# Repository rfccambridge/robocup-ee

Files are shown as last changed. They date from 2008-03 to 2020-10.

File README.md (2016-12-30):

## Build Environment Installation

- Make sure you have clang-format installed: 
  ```
  apt-cache search clang-format
  sudo apt-get install clang-format-<version>
  ```
- `source /opt/ros/kinetic/setup.bash`
- `cd <your robocup directory>/catkin_ws/src`
- `catkin_init_workspace`
- `cd <your robocup directory>/catkin_ws`
- `catkin_make`
- `source <your robocup directory>/catkin_ws/devel/setup.bash`
- Make sure running `echo $ROS_PACKAGE_PATH` prints something similar to `/home/<your_user>/catkin_ws/src:/opt/ros/kinetic/share:/opt/ros/kinetic/stacks`

## Setting Up Your Own Branch To Work In

- `git checkout -b <your name>_branch`
- Now, all changes you make will affect only your environment and no one else's.

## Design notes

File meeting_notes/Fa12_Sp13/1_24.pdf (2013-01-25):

The EE and CS subteams had a meeting on Thursday. Minutes are below, with some relevant notes (section "Mechanical fixes needed") to the ME subteam.

Driving with game controller:

Used remote controller to drive robot. Just use serial control and click "connect to joystick." Make sure it's matched up to the correct robot id.

We noticed strange smell from Jayne, but from River. We couldn't isolate the problem and eventually didn't notice the problem anymore.

Shut-down problem:

At the all-team meeting we noted that a robot would sometimes shut down while driving. We thought it was because the robot was drawing too much current from the batteries when accelerating, thus causing the robots to shut down to avoid permanent damage. We planned to use firmware to limit acceleration.

However, upon further investigation, we found that one robot had this problem only when (1) the kicker board was in and (2) the black cap of the robot was screwed on. This suggests that the cap and kicker board is pushing down and causing a short circuit as the robot is moving, though we're not exactly sure where the sort circuit may be.

We noticed that the boards were wobbly. Rui suggested we hot-glue the boards in at the header pins, so that they're more stable.

More investigation is needed in order to find the exact cause and how to prevent it, and whether this problem only occurs for only that robot, or only that kicker board. EE plans on coming back to Harvard for further trials before the all-team meeting.

Mechanical fixes needed:

- 2 motors are kind of weird - one has a loose gear, the other we may have killed. Both motors are labelled
- 1 robot lacks a plunger for the kicker
- 2 robots don't have the BB set up properly

EE plans on going back on February 9th to test the driving. Is it possible to have these robots - at least the motors - fixed up by then?

Decreasing modularity of electronics:

In the long term, we may need some redesign of the boards. It was suggested to decrease modularity. The boards often don't have too many problems once properly built up, and having fewer boards would decrease the chance for boards randomly touching and short circuiting each other. We would probably hold off the design until after the 2013 competition. Some possible approaches are
- all circuitry on the motherboard
- FPGAs
- PSoC (http://www.cypress.com/?id=1353)

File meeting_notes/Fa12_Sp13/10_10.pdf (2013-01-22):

Minutes:

Recap Last week: Kicker/ Aus
Kicker board – charges caps and sends energy to solenoid (kicker) Auxiliary kicker – a control board that tells the kicker when to kick, when to charge
MOSFET – component used in aux; we use nmos (rather than pmos)
- gate – when voltage between gate and source large enough, current flows from drain to source
- drain
- source

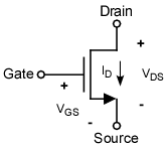
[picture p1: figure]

- further reading: http://en.wikipedia.org/wiki/MOSFET#Modes_of_operation

This week: Brushless
Next Week: firmware

DRC check for eagle tutorial – errors are ok, you'll notice if it is a glaring mistake
ERC – checks schematic versus layout – try to get no errors, which mean that things are not connected; warnings are ok

Brushless board:
– 4 boards on each robot
– each board controls 1 wheel
– communicates with computer to drive wheel – 3 pairs of mosfets
– high side mosfet
– low side mosfet

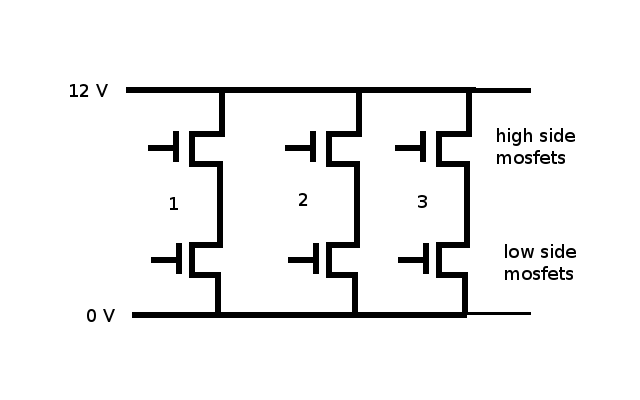
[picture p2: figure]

– can never turn high side and low side mosfet on for the same totem pole
– energizing any pair can get a certain phase

Motor:
– we use brushless motors
– magnet and set of coils
– when a certain set of coils are energized, they induce magnet to go in certain direction
– paste link here for more info
– 3 phases
– hall sensors in motor detect when motor has reached a certain position; will signal that next phase need to be energized

Controlling speed
– You can consider: a variable power source; however, that's difficult to make
– Alternatively: use a 12 volt source, but use a switch to apply the 12 volts for a percentage of the time
– Duty Cycle: the percentage of time the voltage is applied (50% duty cycle for a 12 volt source is equivalent to applying a 6 volt source)

– We keep frequency constant

Oscilloscope Demonstration:
– as the pwm increases, the length of time that the signal is on is longer, also the speed is increased
– note that there are some vias on the board that exist purely as useful probing spots for the oscilloscope probe

Schematic of Brushless Board
– Leftmost panel of schematic shows header pins
– pin2 = 5V
– pin 3, pin4 = QEB, QEA = encoder signals → let us calculate how quickly the motor is going
– BBID0, BBID1 – tells brushless board 1 to do what, tells brushless board 2 what to do; because same signal gets sent to all board (multiplexed), so we need a way to separate the commands
– Hall3, Hall1, Hall2 – hall effect sensors are built into motor; depending on which signal is high, we know which position the motor is in; firmware reads this, and then instructs the mosfets (from the brushless board) to change phase, so that the wheel will turn to another position

Hold on: Hall effect sensor tells us the position information. Encoder also tells us position information. Why both?
Hall effect is very precise – so we use it to tell when to change phases; reducese jittery
Encoder – used to estimate speed and high speed information; in our control loop, we use the encoder to control the speed of the motor

– BOTID0, BITID1, BOTID2, BOTID3 – robot ID;
– question, why do we use 4 ID's?
– For future expansion, so we can suport up to 16 robots. Also, if we ever get 10 robots and want to play them against each other, we can have a unique ID for all of them
– TX, RX – singals, from/to antennae and transmitter
– are signals incripted?
– No, but they are modulated on to carrier frequency
– PH3, PH2, PH1 -
– pin 1, quiet ground – for things that draw small current like microcontroller;
– pin 24, 25 – PE = power ground; draws large current
– if microcontroller is connected to power ground -

Bypass capacitors – supply is noisy; to reduce noise, we add capacitors across ground to act like a low pass filter
Low pass filter:
– http://en.wikipedia.org/wiki/Low-pass_filter#Passive_electronic_realization
– various values: 100 mF and .1 mF in parallel – why?
– B/c 100 mF has bad frequency response (no longer looks like 100 mF at high frequencies, will look like an inductor instead)
– putting 0.1 mF in parallel reduce

Middle Pane:
– microcontroller --- let's ignore this for not

Right pane
– driver – acts as voltage commander
– pins on left receive commands from microcontroller (0-5V)
– pins on right are same signals as commands from microcontroller, but get sent out at 0-12 V – add link to datasheet

Questions
– What are diode and capacitro for
– they are part of a “bootstrap circuit” which help us to get the 12 V exactly
– what are resistors between 12V gate and gate of mosfet for
– limit the current to mosfet; we want to do this b/c the mosfet has a parasitic capacitance in it;
– sense resistor
– monitor current by monitoring voltage across here;

Projects
– Kicker – Erwin, Ben, Manny
– Dribbler – David G, David K, Markus
– Acceleration – Manny, Erwin
– Debugging – Erwin, Markus, Manny, Ben

Timeline
– feb, so that CS has time to implement

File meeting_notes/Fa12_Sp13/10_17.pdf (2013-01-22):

This week in summary: Brief introduction
Next week: take the robot apart and put it back together

Firmware:

(1) Install the following:
IDE: MPLab X
Compiler: XC8, XC16

Get the free versions. If it prompts you for a license key, click "next" and it will ask you to select the free version.

(2) Create a new project (use code from robocup repository):

(2a) The Aux board requires the following project setup:

Family: PIC18F4431
Tools: PICKit2
Compiler: XC8
Right click project once project is created | Add Existing Files
Add these files (and only these files) from robocup-ee/firmware:
- bemixnet.c
- bemixnet.h
- mainLogic_newestBB_no_false_positives.c
- pins.h

(2b) The brushless requires the following project setup: Family: dsPIC30F4011
Tools: PICKit2
Compiler: X16
Right click project once project is created | Add Existing Files
Add these files (and only these files) from robocup-ee/firmware:
- bemix_v2.n
- bemix_v2.h
- main_v2.c
- pins_v2.h

Aux uses 8-bit microcontroller
Brushelss uses 16-bit microcontroller - recently upgraded to nicer (faster) microcontroller

--> microcontrollers have to be programmed slightly differently

Process for loading code onto board:

Note the following:
- on board, there is a 5 pin header pin
- there is a programming cable

Process:
1. plug in board to power (plug it into the robot, with the robot turned on)
2. plug in programmer to the header pin, with the arrow on the programmer pointing to pin 1
3. build project (there is a button in the IDE)
4. program the board (button)
5. toggle power
Order:
Hint: never plug things in backwards! signals go to specific places, and applying the wrong signal to the wrong pin can destroy a board

All brushless boards faces front. Aux board faces front. Kicker board faces the back (to make it fit). Yellow cable to motor. The connector has a set of "tabs" that you need to loosen in order to remove the cable. Silver side faces up.
Encoder cable. You'll notice on the motherboard, the one pin is marked 1, the other pin is marked 4. On the connector, there is line that is marked black or red. make sure the black or red line is matched up to pin 1.

Random question when looking at schematic:
Thermal - a thin traces that connect a component to the main part of the trace. makes it easier to solder b/c there is less heat loss. However, our traces are usually thin enough that we don't have to lose about heat dissipation while soldering.

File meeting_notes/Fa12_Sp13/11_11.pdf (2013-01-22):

Here are notes from today's meeting if you had to leave early or couldn't make it out:

All-team meeting, scrimmage

We plan to have a all-team meeting at Harvard toward the beginning of December to see the robots driving around and to try to get a two-on-two game going on. But for that, we need the following fixed up

- break beams
- auxiliary kickers
Break Beams

The break beams are used to detect when the ball is in front of the kicker, so the robot knows exactly when to kick.

An old system we tried was a reflective break beam sensor. It did not work well because the ball was not so reflective, it was dependent on ambient light conditions, and was sensitive to the ball coming in from a variety of angles.

The current system places the emitter LED and receiver on the left and right side of the ball. The emitter sends infrared light at a certain frequency, which the receiver looks for. When the beam is broken, the receiver sends an active low signal. This is slightly more robust, though we will have to put a lot of effort into placing the emitter and receiver.

Auxiliary Kicker

We ran into some problems demonstrating the break beam boards because the aux kicker boards (which run the firmware for the break beams) have been having trouble (1) getting programmed or (2) receiving signals from serial control.

We believe these problems are due either to (1) faulty chips or to (2) the fact we upgraded our programming IDE and there may be some conflicts. Rui's looking into the IDE, but if he doesn't identify any problems, we'll order a new set of chips and replacing them.

Solenoid

I believe last week Markus and David(?) played around with the kicker. They raised it a bit, so that the center of the kicker hit the ball. A maximum of 4 m/s was attained, doubling the energy being delivered to the ball.

Markus built up a new shaft for the solenoid, which included a magnetic material for the shaft instead of a aluminium. However, when we tried to kick, it didn't work.

Plan for next week:

- debug/rebuilt aux kicker boards
- get break beams working
- test Markus's new designs

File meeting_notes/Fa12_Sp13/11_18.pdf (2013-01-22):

Also, remind me to add you to the MechE list if you want to spy on what they do!

Minutes:

- should be electrically fit for all-team meeting!
- just need to mount breakbeams
- next meeting is in 2 weeks
- keep your repository up to date - pull the changes that we committed today.
- have a great thanksgiving break!

Auxiliary Kicker

- there was a problem with code in the repository, not the the new IDE. When Rui used the old code from the computer (back when we used subversion as a repository), and it worked. Repository is now updated.
- some aux kickers still seem to have a write protection on them, so we have to replace those pics next time

Breakbeam

- works now that the aux board's pic has been fixed!
- added an arbitrary delay before the receiver looks for sensor signal, so that the kicker would not immediately kick.

Dribbler

- when set to 0, the pin PWM4 would output a constant 0V
- when set to anything else, PWM4 would output a constant 5V
- perhaps we're configuring some registers incorrectly?
- to do: read section 15 and 17 of datasheet (PIC18F4331)

For next meeting:

- mount break beams
- replace pics on aux kickers
- figure out the pwm registers to the dribbler
- Markus's solenoid shaft?
- make sure we can assemble a robot with all working components?

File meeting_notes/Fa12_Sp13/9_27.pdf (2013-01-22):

Minutes – 9/23/12 EE Sub-meeting

Eagle
- Download Eagle
- google: “cadsoft eagle”. The first link should bring you to the website.
- under “Downloads” there should be instructions for installing a free version
- There are 2 views
- schematic: pick components and wire them together
- board layout: layout the components as they would be placed on a board
- Eagle will generate files that can be sent out to manufacturers to print circuit boards
- Useful for future projects, in which we might create simple boards to help gather data for other subteams

Git
- Revision Control Software – allows us to concurrently make changes while avoiding conflicts; keeps track of old versions; learn more here: http://gitimmersion.com/
- To get access our git repository, make an account here: http://github.com then send Lisa (liulisa@mit.edu) your username
- If you use windows, you should also download this: http://code.google.com/p/tortoisegit/
- For macs and ubuntu, e-mail Rui or Lisa

Kicker Board
- controls kicking of the ball
- computer commands board to charge capacitor
- takes 2-3 seconds to charge
- audible humming noise b/c the board flips a switch to increase voltage (more explanation on this later, or read wikipedia page on buck converters)
- another computer command sends the energy through a solenoid, which creates a magnetic field, which pushes forward a plunger, which hits the ball
- vaporize resistor demonstration
- Together the capacitors are 3 milliFarads and charge up to 250 V! For capacitors energy = (1/2)*C*V^2 → this is “like getting punched”
- Instead of sending energy to solenoid, we placed a 5 kOhm resistor at the load terminals
- Some equations:
- V = I*Resistance
- Power = I*V
- 12.5 Watts across the resistor which is rated for 0.25 Watts.
- Resistor smoked, then exploded. Remains are yet to be found.
- Discussion about how to repeat the experiment with a hot dog.
- Conclusion: it would be messy
- Takeaway: the capacitors are dangerous
- neon light indicates when capacitors are charged
- use discharge button, hold down for 5 seconds after light goes out before handling robot again

Possible projects
- circuits boards – other subteams need to gather stats
- debugging circuit boards (using oscilloscope)
- firmware?

Next few weeks:

9/30 – More about Kicker/Aux board
10/7 (or maybe later on this 4-day weekend) – Brushless boards 10/14 – Firmware

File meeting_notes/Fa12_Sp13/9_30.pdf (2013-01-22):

Thanks for coming to the meeting today. For those of you who couldn't make it, here are some points from today's meeting:

Think about small projects you want to do to improve the robot
- Suggestions: measuring kicking speed / distribution, optimizing efficiency of energy transfer from capacitors to ball, multiple kickers / chip kicking, optimizing dribbler, optimizing break beam, characterizing robot acceleration
- Work in groups if you want
- Think about small projects you want to do to improve the robot
- Suggestions: measuring kicking speed / distribution, optimizing efficiency of energy transfer from capacitors to ball, multiple kickers / chip kicking, optimizing dribbler, optimizing break beam, characterizing robot acceleration
- Work in groups if you want
- Auxiliary kicker and kicker boards form a subsystem on the robot for charging up the capacitors and kicking the ball
- Auxiliary kicker board communicates with off board computers
- Tells kicker board to charge capacitors / kick ball
- Tells dribbler to turn on/off
- Kicker board controls charging the kicking capacitors and kicking the ball
- Charge the capacitors by storing energy in transformer and dumping onto capacitor
- Kick the ball by dumping energy from capacitors into solenoid
- MOSFETs are switches used to turn on/off current
- MOSFETs have 3 terminals: gate, drain, source
- Raise voltage at gate to turn on switch between drain and source\
Lower voltage at gate to turn off switch

Please do the Eagle tutorial! I've attached the tutorial again in this email. If you still don't have access to the Robocup EE files on Git, I'll show you next meeting.

Next week is a 4-day weekend, and we'll send out a Doodle to see what times people are available. We'll be talking about the brushless boards.

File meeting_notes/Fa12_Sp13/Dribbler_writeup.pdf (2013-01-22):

Dribbler Motor Writeup
Lisa Liu
January 10th, 2013

Purpose: In the Robocup competition, many teams employ a dribbler in order to put backspin on the ball so that the robot controls the ball while moving. Although RFC-Cambridge installed a prototype of the dribbler, it has not yet been used in gameplay. For the Fall '12 semester of Power Electronics (6.131), my final project was to get the dribbler running in response to signals from the microcontroller, so it could put backspin on the game ball.

Background: The dribbler mechanism is composed of a DC dribbler motor and a rubber tube. The tube is placed onto an spinning axis, which is connected to the motor with an elastic band. Therefore, when the motor spins, so does the tube, which spins the ball backward.

The DC motor spins at a rate proportional to the applied voltage. That is, w = k*V, where w is the rotational velocity; k is the motor constant; and V is the voltage applied. We can vary the voltage using a PWM signal.

The PWM signal comes from a microcontroller on the auxilliary kicker board. However, the microcontroller only outputs 0 and 5 V, so there is some additional circuitry on the auxilliary kicker board which buffers the 5 V up to 12 V.

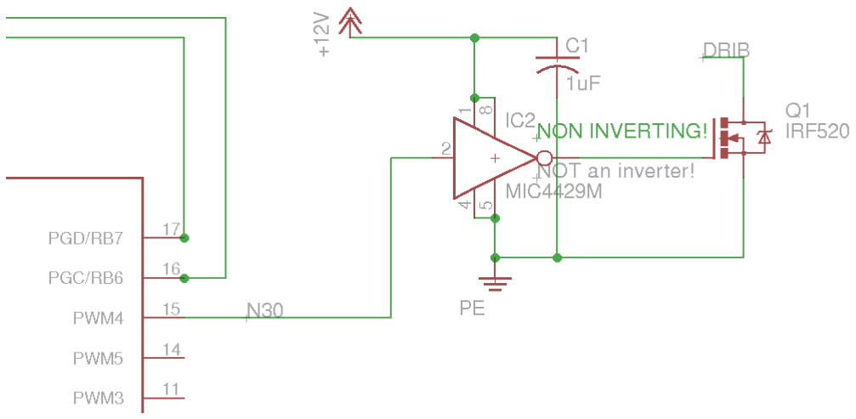
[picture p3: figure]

Figure 1. The microcontroller on the auxillery kicker board outputs a PWM signal from pin 15 (PWM4) which goes to the MIC4429M MOSfet driver. The MIC4429M boosts the 0-5 V signal from the microcontroller up to 12 volts.

The DRIB signal is connected to the motherboard, where the motor terminals are. One terminal is connected to the DRIB (which is relabeled as “DRIB-” on the motherboard schematic). The other terminal is connected to V+, which is the positive terminal of the battery.

In gameplay, we would like the microcontroller to process radio commands. When it receives a command to run the dribbler motor, the dribbler motor will ideally put backspin on the ball.

Problem: There are some mechanical problems with the design. That is, the tube doesn't turn so easily, which may make the load too much for the motor. There are varying sizes of elastics, and not all (*cough* very few) of them are conducive to making the tube spin.

A minor electrical issue was that the motor was not properly speced to the robot. The motor could take voltages up to 24 volts, but the robot provided only 12 volts. Even though the motor could backspin the ball at 12 volts, there was concern that the full potential of the motor was not utilized.

The main problem encountered at the EE submeetings is getting the microcontroller to output a PWM signal at all. We suspected that the microcontroller was incorrectly programmed.

Project:

Boost Converter

In speaking to bakerl from ME, I found out the ME subteam is updating the dribbler design and getting a new motor, which is more properly speced to the robot. This is perhaps the better solution, as building the boost converter requires extra PCB space and relatively large capacitors, which might not fit in the robot and would certainly weigh the robot down. Therefore, this portion of my project is no longer relevant, but may be useful for learning or for future reference.

I built a a boost converter which boosted the voltage to a higher voltage, which depended on the duty cycle according to V_out = V_in /(1-D).

However, the PWM signal only controlled the amount of boosting, and otherwise required the motor to always be connected to the battery. This is unideal because unneeded dribbling will waste battery energy. Therefore, I added a LM555 timer in one-shot monostable mode to act as a switch; when there was no PWM, the motor was disconnected from battery, else it let the PWM signal power the the robot.

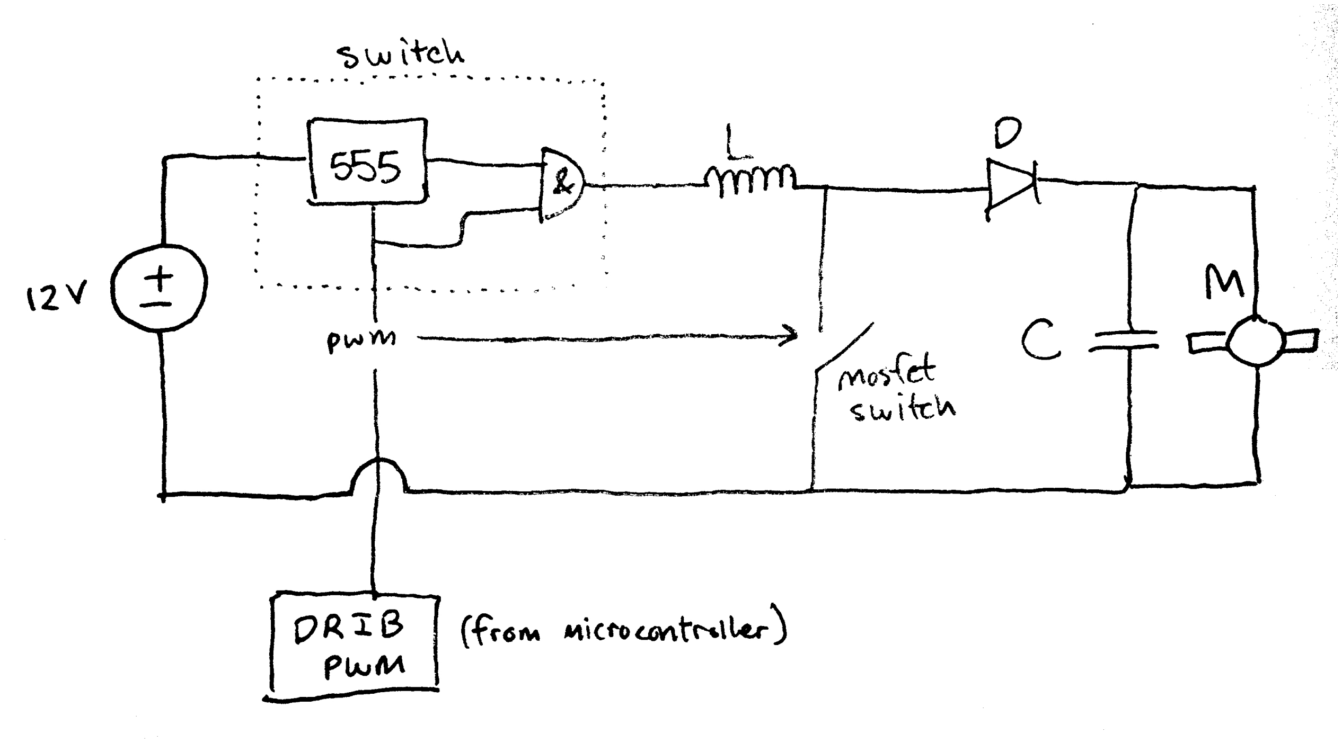
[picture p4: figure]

Figure 2. When the 555 is set up in one-shot monostable mode, it will output a HIGH signal when it detects a falling edge on the input pin. The duration of the HIGH signal depends on an external capacitor and resistor.

Programming the microcontroller:

During subteam meetings, we were unable to successfully program the microcontroller to PWM. The key register that needed to be adjusted was PWMCON0. This register needed to be adjusted so that PDC2 would be in complementary mode. Previously, it was in independent mode, which means that PWM1 would output a signal, but PWM4 would be left hanging. PTPERH, PTCON1, and PDC2L (and perhaps a few other registers) control the frequency and duty cycle of the signal.

In a future implementation of the auxilliary kicker board, it may be simpler to use the pins for PWM1, PWM2, or PWM3, which do not require the complementary mode bit to be set.

Measurement:

During subteam meetings, we tried to measure the output of the microcontroller by placing the oscilloscope probes directly on the V+ and DRIB- terminals. While we noticed V+ always as 12 volts, as expected, however, DRIB- was less consistent.

The problem in our method of measurement is that DRIB- is left hanging. That is, when the PWM signal is HIGH, the MOSfet connects DRIB to ground, which is what we expect. However, when the PWM signal is LOW, the MOSfet leaves DRIB hanging, giving output a signal which is neither HIGH nor LOW. Therefore, we need a pullup resistor in order to measure any sort of meaningful signal.

A naïve thought is to use the resistance of the motor as a pull up resistor. However, as we explore in the next section, directly plugging the motor into the motor terminals doesn't work.

Motor:

When I used a pull up resistor on the DRIB terminal, the output of the microcontroller was a PWM signal exactly as we want it to be. However, when we use a motor instead of a resistor, the output looks extremely irregular.

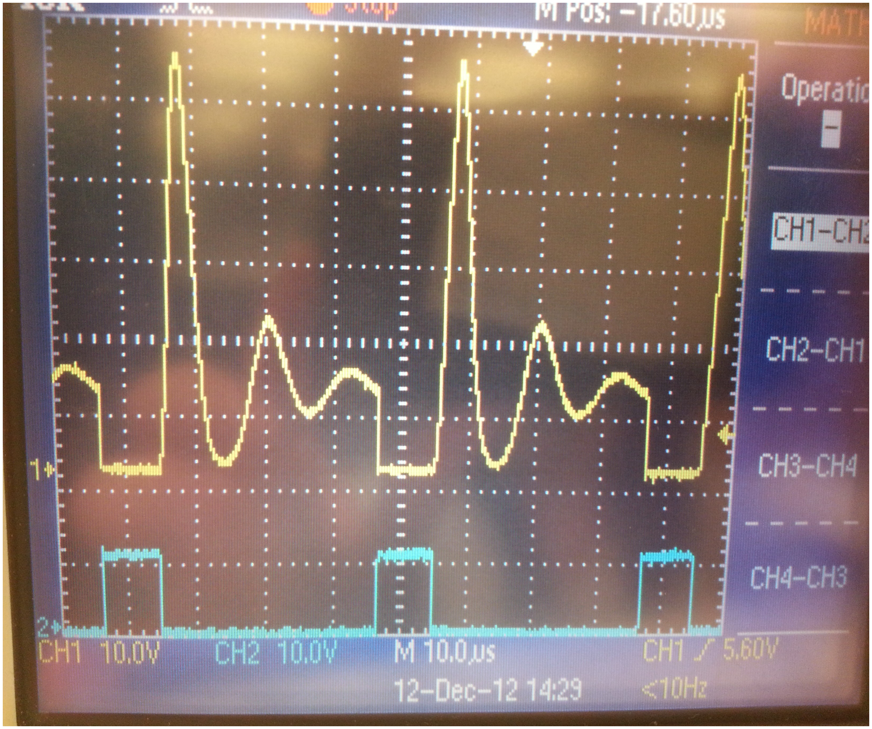
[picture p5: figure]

Figure 3. The blue signal is the signal between the MOSfet driver and the MOSfet. The yellow signal is the voltage across the motor; it reaches voltages up to 50 volts and displays significant oscillations.

The oscillations are due the th inductance of the motor, which creates an LRC circuit. This adds reasonance and oscillation to the circuit, explaining the 50 V peak and the inability of the DC motor to operate properly.

Therefore, a diode should be placed across the motor, between the DRIB- and V+ terminals, facing the DRIB- terminal, in order to stop the capacitor from charging and creating the reasonant circuit.

Conclusion:

A boost converter is not needed. But perhaps in future implementations of the boards, the following changes should be made:

- Auxillery board should be use PWM1, PWM2, or PWM3, before using PWM4.
- Motherboard should put a diode across the dribbler terminals.

A boost converter is not necessary, since it seems 12 V is enough to provide backspin on the ball. We will leave it up to the ME subteam to get the ball rolling.

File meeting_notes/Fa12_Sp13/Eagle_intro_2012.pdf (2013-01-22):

Getting

to

know

Eagle

1. Download

(http://www.cadsoft.de/freeware.htm)

and

install

Eagle.
2. We

are

going

to

design

in

Eagle

a

board

to

test

the

kicker

board.

Here

is

the

circuit

that

we

will
work

with:

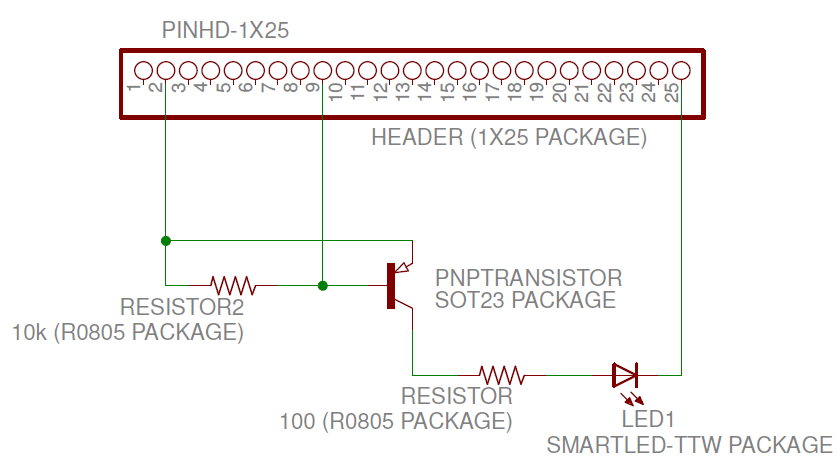
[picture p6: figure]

The

rectangle

with

25

pins

at

the

top

is

a

set

of

header

pins

similar

to

the

header

pins

on

each
board

that

plugs

into

the

motherboard

on

the

robot.

Pin 2

is

a 5V

supply

pin,

pin

9

is

called

the
DONE

pin,

and pin

25

is

the

ground

(0V)

pin.

This

circuit

is

supposed

to

turn

on

the

LED

when

the
kicker

board

finishes

charging

the

capacitors.

Before

the

capacitors

are

done

charging,

pin

9

is

at
5V.

After

the

capacitors

are

done

charging,

pin

9

goes

down

to

0V,

which

turns

on

the

PNP
transistor.

The

PNP

transistor

acts

like

a

switch.

When

the

left

terminal

is

at

5V,

the

switch

is

off.
When

the

left

terminal

is

at

0V,

the

switch

is

on,

which

allows

current

to

flow

in

the

direction

of
the

arrow,

from

the

top

terminal

to

the

bottom

terminal.

In

our

case,

current

flows

from

pin

2,
through

the

PNP

transistor,

through

the

LED,

to

pin

25.

This

turns

on

the

LED

when

the
capacitors

are

done

charging.

In

this

project,

we

will

create

this

circuit

in

Eagle

and

design

a

printed

circuit

board

(just

like

the
boards

that

go

into

the

robots

right

now).

Circuit

Schematic

a. Open

up

Eagle

and

select

File

-‐>

Open

-‐>

New

Schematic
b. Add

all

of

the

parts

in

this

circuit

to

the

schematic

using

the

Add tool

(looks

like

a

“D”)

on
the

left toolbar.

Each

part

in

the

diagram

above

has

a

part

name

and

a

package

name.

In

the

Add tool

you

should

search

for

the

part

name

and

then

select

the

part

that

has

the

same
package.
a. After

you

have

found

the

part,

you

may

double

click

on

it

and

it

will

show

up

in

the
schematic.

Click

to

place

the

part

where

you

want

it.

You

can

rotate

the

part

before
placing

it

down

by

right

clicking.
b. At

any

time,

you

may

press

Escape

to

exit

the

tool.
c. To

move

any

item

after it

has

been

placed,

use

the

Move tool.

To

rotate

any

item,

first
select

it

using

the

Move tool

and

right

click

to

rotate

it

90

degrees.
a. Each

item

may

be

selected

using

any

tool

by

clicking

on

the

item’s associated
crosshair.

Notice

that

each

item

has

a

crosshair.

Don’t

just

click

on

the

item

itself,
because

while

most times

the

crosshair

for

the

item

is

in

the

center

of

the

item,
many

times

it

is

not.
b. If

you

click

too close

to

more

than

one

crosshair,

Eagle

does

not

know

which

item
you

selected.

In

this

case,

Eagle

will

highlight

one

of

the

items

it

thinks

you

selected.
If

that

is

the

item

you

want,

left

click

again.

If

not,

right

click

and

Eagle

will

highlight
another

item

it

thinks

you

selected.
d. You

can

find

and

edit

the

name/value

of

any

item

by

using

the

Info tool

(looks

like

an

“i”)
and

clicking

on

the

item.
a. After

clicking

on

any

item,

in

the

Properties window,

you

can

select

the

Smashed
option

to

separate

the

item

and

its

name/value

as

separate

items.

Then,

you

may
move

the

name

or

value

of

the

item

independently

of

the

item

itself

(note

that

the
name

and

value

will

have

individual

crosshairs).
e. You

may

duplicate

an

item

by

using

the

Copy tool

and

clicking

on

the

item

you

want

to
duplicate.

Note

that

you

should

use

the

Info tool

to

change

the

name/value

of

the
duplicated

item

to

something

unique.
f. Add

wires

as

shown

in

the

diagram

using

the

Wire (looks

like

a

diagonal

line)

tool.

At

any
time,

you

may

press

Escape

to

exit

the

tool

and

stop

drawing

more

wires.
a. The

wires

should

connect

appropriately.

To

check

that

two

wires

are

connected,
make

sure

they

have

the

same

names

using

the

Info tool.
b. You

can

force

two

intersecting

wires

to

be

connected

by

using

the

Junction tool
(looks

like

a

green

dot).

In

the

diagram,

I

have

placed

two

green

dots

at

two
different wire

intersections

to

force

a

connection.

Board

Layout

After

creating

the

circuit

schematic,

click

on

the

Board button

at

the

top

to

switch

to

board

view.
(Create

a

new

board

if

Eagle

asks

you

to.)

You

will

see

all

the

parts

that

you

placed

in

your

circuit
in

the

board

view

also,

except:
1) They

are

not

connected
2) They

are

arranged

in

a

mess
We

want

to

lay

out

a

printed

circuit

board

that

neatly

arranges the

parts

and

connects

them
together

using

traces (printed

wires).

Our

board

will

be

.5in

tall

by

2.5in

long

and

have

two

layers.

The

top

layer

will

consist

of

the

traces

that

connect

our

parts,

and

the

bottom

layer

will
be

entirely

a

ground

layer.

Below

is

a

diagram

of

the

completed

board.

a. Use

the

Move tool

to

move

the

sides

of

the

white

box

so

that

the

box

has

dimensions

.5in
by

2.5in.

This

white

box

is

the

extent

of

our

board.

You

may

not

place

anything

outside

this
box

– it

will

not

be

considered

when

the

design

is fabricated!
b. Arrange

the

parts

inside

the

white

box

as

shown

in

the

diagram.

Remember

that

you

can
rotate

any

part

by

using

the

Move tool

and

right

clicking.
a. There

will

be

a

bunch

of

yellow

lines

between

the

parts.

These

are

where
connections

will

be

made,

as

indicated

by

your

circuit

schematic.

Rotate

and

place
each

part

so

that

none

of

the

yellow

lines

cross

(that

way,

your

connections

will

not
cross).
c. Now

we

will

add

the

red

traces.

These

traces

are

all

on

the

top

layer.
a. Click

on

the

Route tool

(looks

like

a

red

trace).

Notice

that

on

the

top

bar

the
leftmost

drop-‐down

menu

currently

has

“1

Top”

selected.

So

we

are

working

with
the

top

layer.
b. On

that

bar,

there

is

another

dropdown

menu

called

Width.

That’s

how

wide

we
want

our

traces

to

be.

In

this

case,

we

want

all

our

traces

to

be

width

0.05.
c. Connect

all

of

the

parts

according

to

the

yellow

lines

by

clicking

on

one

end

of

the
yellow

line

and

then

clicking

on

the

other

end.

You

can

change

how

the

traces

bend
by

clicking

the

appropriate

button

on

the

top

bar.
d. For

now,

do

not

connect

the

LED

to

the

ground

pin.

We

will

use

a

different

type

of
connection

for

that

one.
d. Now

we

will

add

in

the

second

layer

(ground

layer).

Big

ground

layers

are

helpful

for

at

least
two

reasons:
1) Things

are

more

stable

when

there

is

a

lot

of

ground
2) It

makes

laying

out

our

board

easier,

because

if

we

have

anything

that

we

need

to
connect

to

ground,

instead

of

routing

a

long

trace

from

there

to

a

ground

pin,

we

can
just

punch

a

hole

through

the

board

and

access

the

ground

layer,

as

we

will

do

later.
We

will

create

the

ground

layer

using

the

Polygon tool.
a. With

the

Polygon tool

selected,

on

the

top

bar

change

the

“1

Top”

layer

to

the

“16
Bottom”

layer.
b. Trace

out

the

boundaries

of

the

ground

layer.

Notice

that

the

boundaries

include
the

rightmost

header

pin.

In

the

robot,

this

pin (actually,

the

rightmost

three

pins)
connects to

ground.

c. Click

on

the

Ratsnest tool

(looks

like

a

green

X).

The

polygon

will

be

filled

in

blue.
d. Next,

we

need

to

define

that

the

polygon

we

created

is

actually

ground.

Back

in

the
circuit

schematic,

use

the

Info tool

to

find

the

name

of

any

wire

that

connects

to

the
ground

pin.

We

must

change

the

name

of

the

polygon

to

that

name.

(In

general,
everything

that

is

connected

together

will

have

the

same

name).
e. In

the

board

view,

click

the

Name tool

(has

the

writing

“R2

10k”

on

it).

Then

click

on
the

polygon

and

change

the

name.

When

you

click

on

any

item

with

the

Name tool,
Eagle

will

highlight

all

items

that

are

connected

to

it.

Click

on

the

Ratsnest tool

again
to

update

your

change.
e. Now

we

will

connect

the

LED

to

ground

by

punching

a

hole

between

the

top layer

and
bottom

layer.

In

the

actual

created

board,

these

holes

will

be

lined

with

metal

so

anything
touching

the

hole

on

the

top

layer

will

be

connected

with

anything

touching

the

hole

on

the
bottom

layer.

These

holes

are

called

vias.
a. Click

on

the

Via tool,

and

select

a

round

via

on the

top

bar

(middle

option).

Then
click

to

place

the

via

connected

to

one

pad

of

the

LED.
b. We

need

to

define

the

name

of

the

via

so

that

Eagle

can

know

to

connect

the

via

to
ground.

As

you

did

in

the

previous

step,

use

the

Name tool

to

change

the

name

of
the

via

to

the

correct

name.

Click

the

Ratsnest tool

to

update

your

change.
f. At

this

point,

there

should

be

no

more

yellow

lines.

Everything

should

be

arranged

and
connected

correctly.

A

couple

notes:
a. All

of

the

words

describing

the

names/values

of

the

parts

in

board

view

will

be
printed

out

on

the

actual

fabricated

board.

Thus,

you

want

to

be

careful

what

and
where

these

words

are.

Generally,

you

want

to

include

abbreviated

names

of

the
parts

(like

“R2”

for

resistor

2)

and

values

of

the

parts

(like

100

or

10uF)

and

place
these

labels

on

the

board

where

they

won’t

get

covered

up

by

parts

you

solder

on.
We

call

these

labels

silkscreen

labels.

(Notably,

for

descriptive

reasons,

the
silkscreen

labels

in

my

board

layout

example

are

not

good

style

because

they

are
too

long

and

there

are

no

part

value

labels.)

To

change

the

labels

of

an

item in
board

view,

use

the

Info tool

and

click

on

the

item

to

bring

up

the

Properties
window.

You

can

also

check

the

Smashed box

in

the

Properties window

to

separate
the

labels

from

the

item

so

you

may

move

or

delete

them

independently.

To

delete
a

label,

use

the

Delete tool

(looks

like

a

black

X)

and

click

on

the

label. Notice

that

if
you

change

a

label,

the

corresponding

label

in

the

circuit

schematic

also

changes.
b. You

cannot

delete

any

items

except

labels

using

the

Delete tool in

board

view.

If

you
do

so,

an

error

message

will

show

saying

“Cannot

backannotate

this

operation!”

You
can

only

delete

parts

in

the

circuit

schematic.

As

for

traces

and

polygons,

you

may
use

the

Ripup tool

(to

the

right

of

the

Route tool)

to

click

on

and

delete

the
connection.

After

you

do

so,

a

yellow

line

showing

a

needed

connection

will
reappear.
3. After

you

are

finished

with

your

circuit

schematic

and

board

layout,

save

your

project

and

email
it

to

me

(rjin@mit.edu)

so

I

can

take

a

look

at

it.

Thanks

and

good

luck!

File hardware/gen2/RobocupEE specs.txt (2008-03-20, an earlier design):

{\rtf1\mac\ansicpg10000\cocoartf824\cocoasubrtf440
{\fonttbl\f0\fswiss\fcharset77 Helvetica;\f1\fswiss\fcharset77 Helvetica-Bold;}
{\colortbl;\red255\green255\blue255;}
{\*\listtable{\list\listtemplateid1\listhybrid{\listlevel\levelnfc23\levelnfcn23\leveljc2\leveljcn2\levelfollow0\levelstartat1\levelspace360\levelindent0{\*\levelmarker \{disc\}}{\leveltext\leveltemplateid0\'02\'05.;}{\levelnumbers\'01;}}{\listname ;}\listid1}
{\list\listtemplateid2\listhybrid{\listlevel\levelnfc23\levelnfcn23\leveljc2\leveljcn2\levelfollow0\levelstartat1\levelspace360\levelindent0{\*\levelmarker \{disc\}}{\leveltext\leveltemplateid0\'02\'05.;}{\levelnumbers\'01;}}{\listlevel\levelnfc23\levelnfcn23\leveljc2\leveljcn2\levelfollow0\levelstartat1\levelspace360\levelindent0{\*\levelmarker \{hyphen\}}{\leveltext\leveltemplateid1\'02\'05.;}{\levelnumbers\'01;}}{\listname ;}\listid2}}
{\*\listoverridetable{\listoverride\listid1\listoverridecount0\ls1}{\listoverride\listid2\listoverridecount0\ls2}}
\margl1440\margr1440\vieww24280\viewh15120\viewkind0
\pard\tx720\tx1440\tx2160\tx2880\tx3600\tx4320\tx5040\tx5760\tx6480\tx7200\tx7920\tx8640\ql\qnatural\pardirnatural

\f0\fs24 \cf0 Kicker not working wrong mode?\
Prioritze.\
\
\
\
\
\pard\tx720\tx1440\tx2160\tx2880\tx3600\tx4320\tx5040\tx5760\tx6480\tx7200\tx7920\tx8640\ql\qnatural\pardirnatural

\f1\b \cf0 Brushless:
\f0\b0 \
Fault pin from Mosfet driver to PIC with resistor and zener diode.\
current sense hooked up for mosfet driver\
Detect bad encoders and bad hall sensors.\
rev. 3 updated with edits (capacitors)\
move LEDs farther apart.\
only transmit data when requested\
increase transmit speed.\
on header connected to 5v\
Pins:\
ground\
+5\
+12(battery)\
encoder1\
encoder2\
hall1\
hall2\
hall3\
motor1\
motor2\
motor3\
Transmit, \
enable transmit (float if not transmitting, pull low if transmitting) or vice versa, so that transmitter is only on when there is data to be transmitted.\
receive pin to receive radio commands.\
brushless motor id bit0 (set in hardware on motherboard)\
brushless motor id bit1\
Robot id bit0 (from switch on motherboard)\
Robot id bit 1\
Robot id bit 2\
Robot id bit 3\
\
\
\

\f1\b Kicker:
\f0\b0 \
Will have charging and discharging circuitry,\
Connect through the header to Capacitors(which are on the motherboard) and to the 3 solenoids(which will plug into the motherboard).\
	One solenoid for main kicker. The other two solenoids in series (Walker in favor of Ben mostly agrees Kyle less sure). Should do math to check series better than parallel.\
2 powers of kicking.\
A header pin that can take high current and high voltage.\
Each power trace coupled with its own ground. (Both solenoid wires should go to the kicker board so current \
\
Pins:\
capacitor1 +\
cap1 -\
cap2 +\
cap2 -\
main inductor +\
main inductor -\
inductor pair +\
inductor pair -\
------\
+5\
ground\
+ 12(battery voltage)\
kick main solenoid 1/2 strength\
kick main solenoid full strength\
kick chip solenoids 1/2 strength\
kick chip solenoids full strength\
enable charging (charging when high)\
discharge through power resistor when high\
\

\f1\b Auxillery Kicker Board\
\pard\tx720\tx1440\tx2160\tx2880\tx3600\tx4320\tx5040\tx5760\tx6480\tx7200\tx7920\tx8640\ql\qnatural\pardirnatural

\f0\b0 \cf0 a few indicator LEDs\
Pins:\
Dribbler +\
Dribbler -\
Photo diode +\
photo diode -\
photo LED\
kick main solenoid 1/2 strength\
kick main solenoid full strength\
kick chip solenoids 1/2 strength\
kick chip solenoids full strength\
enable charging (charging when high)\
discharge through power resistor when high\
cap1 voltage (0-5v) [from voltage divider on motherboard]\
cap2 voltage (0-5v) [from voltage divider on motherboard]\
transmit\
transmit enable\
receive\
ground\
+5\
+12(battery)\
Robot id bit0\
Robot id bit 1\
Robot id bit 2\
Robot id bit 3\
\
Variable speed dribbling in one direction\
Receives and parses radio commands to control kicker. Send back any relevant information.\
\
\
\pard\tx720\tx1440\tx2160\tx2880\tx3600\tx4320\tx5040\tx5760\tx6480\tx7200\tx7920\tx8640\ql\qnatural\pardirnatural

\f1\b \cf0 \
\
\pard\tx720\tx1440\tx2160\tx2880\tx3600\tx4320\tx5040\tx5760\tx6480\tx7200\tx7920\tx8640\ql\qnatural\pardirnatural

\f0\b0 \cf0 \
\
\pard\tx720\tx1440\tx2160\tx2880\tx3600\tx4320\tx5040\tx5760\tx6480\tx7200\tx7920\tx8640\ql\qnatural\pardirnatural

\f1\b \cf0 Motheboard:
\f0\b0 \
Power switch\
Robot ID selector switches\
\

\f1\b Radio:
\f0\b0 \
Communication each board.\
\pard\tx220\tx720\tx1440\tx2160\tx2880\tx3600\tx4320\tx5040\tx5760\tx6480\tx7200\tx7920\tx8640\li720\fi-720\ql\qnatural\pardirnatural
\ls1\ilvl0\cf0 3 communication pins:\
\pard\tx720\tx1440\tx2160\tx2880\tx3600\tx4320\tx5040\tx5760\tx6480\tx7200\tx7920\tx8640\ql\qnatural\pardirnatural
\cf0 1. Transmit, \
2. enable transmit (float if not transmitting, pull low if transmitting) or vice versa, so that transmitter is only on when there is data to be transmitted.\
receive pin to receive radio commands.\
Gyro board when plugged in, can intercept radio commands change if needed and retransmit.\
The USB and radios will go to the Gyro board, which will then send things on to the rest of the robot.\
Transmitter and receiver on Motherboard with better (bigger) antennas. \
Have a usb hub with built in usb to serial convertor. (transmit is always connected to USB Receive is switch activated)\
Radio Channel Selector for transmitter and receiver.\
Switch to switch between listening to radios and listening to the usb Hub.\
\
2 Capacitors soldered on directly.\
\
Connectors:\
each battery pack\
3 solenoid\
1 dribbler\
photodiode\
breakbeam LED\
4 motor\
4 encoder (probable)\
4 Brushless headers\
1 Auxiliary Kicker header\
1 Kicker header\
1 Gryo board header\
1 USB connector\
3 Widgets(Kyle)\
\
Indicators:\
Power on\
LED's from Voltage monitor \
Neon for each capacitor.\
LED's for transmit, receive, and transmit enabled lines (just wired across serial through a buffer).\
\
\
Switching Regulator:\
step down battery voltage to +5\
\
Voltage dividers for each capacitor:\
Resistor voltage divider and buffer(Op amp) to Auxiliary brushless board.\
\
 Voltage monitor:\
(comparator with voltage divider) Yellow-Low Red-Dead.\
\
\
\pard\tx940\tx1440\tx2160\tx2880\tx3600\tx4320\tx5040\tx5760\tx6480\tx7200\tx7920\tx8640\li1440\fi-1440\ql\qnatural\pardirnatural
\ls2\ilvl1\cf0 \
\
\pard\tx940\tx1440\tx2160\tx2880\tx3600\tx4320\tx5040\tx5760\tx6480\tx7200\tx7920\tx8640\li1440\fi-1440\ql\qnatural\pardirnatural
\ls2\ilvl1
\f1\b \cf0 Power:
\f0\b0 \
Battery voltage should be between 12 and 20v so can drive the motors as is.\
Need to handle 5Amps peak draw and ?????Ah\
\
separate power regulated(+12) and or bipassed for ICs, current limit motors.\
\
\ls2\ilvl1
\f1\b Gyro board:\
\pard\tx940\tx1440\tx2160\tx2880\tx3600\tx4320\tx5040\tx5760\tx6480\tx7200\tx7920\tx8640\li1440\fi-1440\ql\qnatural\pardirnatural
\ls2\ilvl1
\f0\b0 \cf0 Gyro board will serve as a bridge between the usb and radio, and the rest of the boards(if it wants for now just a dummy board)\
Has a Pic, some indicator LED's and a Gyro and related circuitry.\
How position and orient board?\
\
Pins:\
+5\
+12\
ground\
receive data in\
receive data out\
transmitter enable in\
transmitter enable out\
transmitter enable in\
transmitter enable out\
\
\pard\tx940\tx1440\tx2160\tx2880\tx3600\tx4320\tx5040\tx5760\tx6480\tx7200\tx7920\tx8640\li1440\fi-1440\ql\qnatural\pardirnatural
\ls2\ilvl1
\f1\b \cf0 \
\pard\tx940\tx1440\tx2160\tx2880\tx3600\tx4320\tx5040\tx5760\tx6480\tx7200\tx7920\tx8640\li1440\fi-1440\ql\qnatural\pardirnatural
\ls2\ilvl1
\f0\b0 \cf0 \
\
\
Board sizes and side header pins are on.\
\
Find specs for 2 smaller solenoids take 400v?}

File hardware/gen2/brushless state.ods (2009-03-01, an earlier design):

ID | Revision | State | Change | Date of Change
11 | 5 | appears to work on stationary robot
13 | 5 | Ignores radio, even though signal is present at RX pin. PIC is probably bad
19 | 5 | appears to work on a stationary robot
20 | 5 | appears working on stationary robot
21 | 5 | appears working on stationary robot
22 | 5 | appears to work on stationary robot
22 | 5 | Dead spot, appears to be a broken mosfet driver | replaced mosfet driver | 02/28/09
23 | 5 | appears working on stationary robot
bb06 | 4 | appears to work on stationary robot
BB07 | 4 | appears working on stationary robot

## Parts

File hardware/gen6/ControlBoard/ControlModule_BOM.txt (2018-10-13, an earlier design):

Partlist exported from C:/Users/joncr_000/robocup/robocup-ee/hardware/gen5/ControlBoard/ControlModule.sch at 12/26/2016 15:41:58

Part    Value         Device           Package               Description                                             MF MPN           OC_FARNELL OC_NEWARK PACKAGE PROD_ID    SUPPLIER VALUE        
3.3REG  3.3REG1AREG   3.3REG1AREG      DPAK                                                                                                                                                         
C4      47uF          CAP1206          1206                  Capacitor                                                                                                                              
C5      1uF           CAP0805          0805                  Capacitor                                                                                                                              
C6      0.01uF        CAP0805          0805                  Capacitor                                                                                                                              
C7      0.01uF        CAP0805          0805                  Capacitor                                                                                                                              
C8      10uF          CAP0805          0805                  Capacitor                                                                                                                              
C9      0.1uF         CAP0805          0805                  Capacitor                                                                                                                              
C10     47uF          CAP1206          1206                  Capacitor                                                                                                                              
C11     0.01uF        CAP0805          0805                  Capacitor                                                                                                                              
C12     1uF           CAP0805          0805                  Capacitor                                                                                                                              
C13     1uF           CAP0805          0805                  Capacitor                                                                                                                              
C14     0.1uF         CAP0805          0805                  Capacitor                                                                                                                              
FRAME1  FRAME-LETTER  FRAME-LETTER     CREATIVE_COMMONS      Schematic Frame                                                                                                                        
PWR_LED               LED1206          LED-1206              LEDs                                                                                                                                   
Q1      BSS123        BSS123           SOT23                 N-CHANNEL MOS FET                                                                                                                      
Q2      BSS123        BSS123           SOT23                 N-CHANNEL MOS FET                                                                                                                      
R1      100           RESISTOR0805-RES 0805                  Resistor                                                                                                                               
R2      10k           RESISTOR0805-RES 0805                  Resistor                                                                                                                               
R3      0             RESISTOR0805-RES 0805                  Resistor                                                                                                                               
R4      0             RESISTOR0805-RES 0805                  Resistor                                                                                                                               
R5      10k           RESISTOR0805-RES 0805                  Resistor                                                                                                                               
R6      100           RESISTOR0805-RES 0805                  Resistor                                                                                                                               
R7      100           RESISTOR0805-RES 0805                  Resistor                                                                                                                               
R8      10k           RESISTOR0805-RES 0805                  Resistor                                                                                                                               
R9      10k           RESISTOR0805-RES 0805                  Resistor                                                                                                                               
R10     100           RESISTOR0805-RES 0805                  Resistor                                                                                                                               
R13     1k            RESISTOR0805-RES 0805                  Resistor                                                                                                                               
R14     1k            RESISTOR0805-RES 0805                  Resistor                                                                                                                               
R15     1k            RESISTOR0805-RES 0805                  Resistor                                                                                                                               
R16     1k            RESISTOR0805-RES 0805                  Resistor                                                                                                                               
RX      TEST_PT       TEST_PT          TESTING_PT            Testing Point                                                                                                                          
RX_LED                LED1206          LED-1206              LEDs                                                                                                                                   
S2      TAC_SWITCHSMD TAC_SWITCHSMD    TACTILE-SWITCH-SMD    Momentary Switch                                                                                      SWCH-08247          TAC_SWITCHSMD
S4      TAC_SWITCHSMD TAC_SWITCHSMD    TACTILE-SWITCH-SMD    Momentary Switch                                                                                      SWCH-08247          TAC_SWITCHSMD
SCK_LED               LED1206          LED-1206              LEDs                                                                                                                                   
SV1     ICSP          MA03-2           MA03-2                PIN HEADER                                                               unknown    unknown                                            
SV2                   MA10-1W          MA10-1W               PIN HEADER                                                               unknown    unknown                                            
SV3                   MA10-1W          MA10-1W               PIN HEADER                                                               unknown    unknown                                            
TX      TEST_PT       TEST_PT          TESTING_PT            Testing Point                                                                                                                          
TX_LED                LED1206          LED-1206              LEDs                                                                                                                                   
U$1     4-POS-DIP     4-POS-DIP        4-POS-DIP-SMD         4 Position DIP Switch                                                                                 SWCH-12418                       
U$2     INDUCTOR      INDUCTOR         0805                                                                                                                                                         
U1      ATMEGA328P-AU ATMEGA328P-AU    QFP80P900X900X120-32N 8-bit Microcontroller with In-System Programmable Flash    ATMEGA328P-AU 1715486    14R4631   TQFP-32            Atmel                 
XBEE    XBEE-1B1      XBEE-1B1         XBEE-1                Xbee module footprints

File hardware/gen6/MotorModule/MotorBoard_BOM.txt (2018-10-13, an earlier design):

Partlist exported from C:/Users/joncr_000/robocup/robocup-ee/hardware/gen5/MotorModule/MotorBoard.sch at 12/26/2016 16:16:32

Part        Value              Device             Package          Description               MF MPN             OC_FARNELL OC_NEWARK PROD_ID   
C1          1uF                CAP0805            0805             Capacitor                                                                   
C2          100uF              CAP-POLAR          PANASONIC_D      Cap Alum Polarized                                                CAP-10547 
C3          .1uF               CAP0805            0805             Capacitor                                                                   
C4          1uF                CAP0805            0805             Capacitor                                                                   
C5          .1uF               CAP0805            0805             Capacitor                                                                   
C6          0.1uF              CAP0805            0805             Capacitor                                                                   
C7          100uF              CAP-POLAR          PANASONIC_D      Cap Alum Polarized                                                CAP-10547 
C8          .1uF               CAP0805            0805             Capacitor                                                                   
C12         .1uF               CAP0805            0805             Capacitor                                                                   
C13         0.1uF              CAP0805            0805             Capacitor                                                                   
D5          DIODE-ZENERDO214AC DIODE-ZENERDO214AC DO214AC          Zener Diode                                                                 
FRAME7      FRAME-LETTER       FRAME-LETTER       CREATIVE_COMMONS Schematic Frame                                                             
GEN_5_REV_A Fall 2016          LOGO               LOGO                                                                                         
IC2         3.3V REG           LT1129CST5         SOT223           VOLTAGE REGULATOR            LT1129CST-5#PBF 1663375    57M2069             
J1          M20X2SHROUDED      M20X2SHROUDED      2X20_SHROUDED    0.1" spaced headers                                               CONN-12263
LED9                           LED1206            LED-1206         LEDs                                                                        
LED11                          LED1206            LED-1206         LEDs                                                                        
LED13                          LED1206            LED-1206         LEDs                                                                        
LED15                          LED1206            LED-1206         LEDs                                                                        
Q1                             N-MOSFET           DPAK             N-Channel Power Mosfet                                                      
Q2                             N-MOSFET           DPAK             N-Channel Power Mosfet                                                      
Q3                             N-MOSFET           DPAK             N-Channel Power Mosfet                                                      
Q4                             N-MOSFET           DPAK             N-Channel Power Mosfet                                                      
Q5                             N-MOSFET           DPAK             N-Channel Power Mosfet                                                      
Q6                             N-MOSFET           DPAK             N-Channel Power Mosfet                                                      
R1          1k                 RESISTOR0805-RES   0805             Resistor                                                                    
R2          4.7k               RESISTOR0805-RES   0805             Resistor                                                                    
R3          4.7k               RESISTOR0805-RES   0805             Resistor                                                                    
R4          4.7k               RESISTOR0805-RES   0805             Resistor                                                                    
R6          240                RESISTOR0805-RES   0805             Resistor                                                                    
R7          1k                 RESISTOR0805-RES   0805             Resistor                                                                    
R8          240                RESISTOR0805-RES   0805             Resistor                                                                    
R9          1k                 RESISTOR0805-RES   0805             Resistor                                                                    
R10         240                RESISTOR0805-RES   0805             Resistor                                                                    
R12         240                RESISTOR0805-RES   0805             Resistor                                                                    
R13         240                RESISTOR0805-RES   0805             Resistor                                                                    
R14         240                RESISTOR0805-RES   0805             Resistor                                                                    
R16         2K                 RESISTOR0805-RES   0805             Resistor                                                                    
R17         2K                 RESISTOR0805-RES   0805             Resistor                                                                    
R18         0.05               R-US_R2512         R2512            RESISTOR, American symbol                                                   
R63         1k                 RESISTOR0805-RES   0805             Resistor                                                                    
R99         1k                 RESISTOR0805-RES   0805             Resistor                                                                    
R101        1k                 RESISTOR0805-RES   0805             Resistor                                                                    
R103        1k                 RESISTOR0805-RES   0805             Resistor                                                                    
U$1         DRV8307            DRV8307            QFN40-6X6                                                                                    
U$2         INDUCTOR           INDUCTOR           0805

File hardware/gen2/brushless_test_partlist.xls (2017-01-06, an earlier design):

Part # | Distr # | Web | Description | Package | Quantity | Price(1) | Total
A3938SLDTR-T | 620-1130-1-ND | Digikey | Drivers Chip | TSSOP | 1 | 5.94 | 5.94
IRF720B | 512-IRF720B | Mouser | MOSFET | TO-220 | 6 | 0.86 | 5.16
PT6KV-02300-PT6KV-202A2020 | 531-PT6KV-2K | Mouser | Variable Resistor |  | 1 | 0.28 | 0.28
Resistors
Value | Quantity
0 | 1
10 | 6
1k | 1
5.1k | 1
20k | 1
40k | 1
50k | 1
Capacitors
Value | Quantity
0.001u | 1
0.1u | 7
10u | 2
100u | 1

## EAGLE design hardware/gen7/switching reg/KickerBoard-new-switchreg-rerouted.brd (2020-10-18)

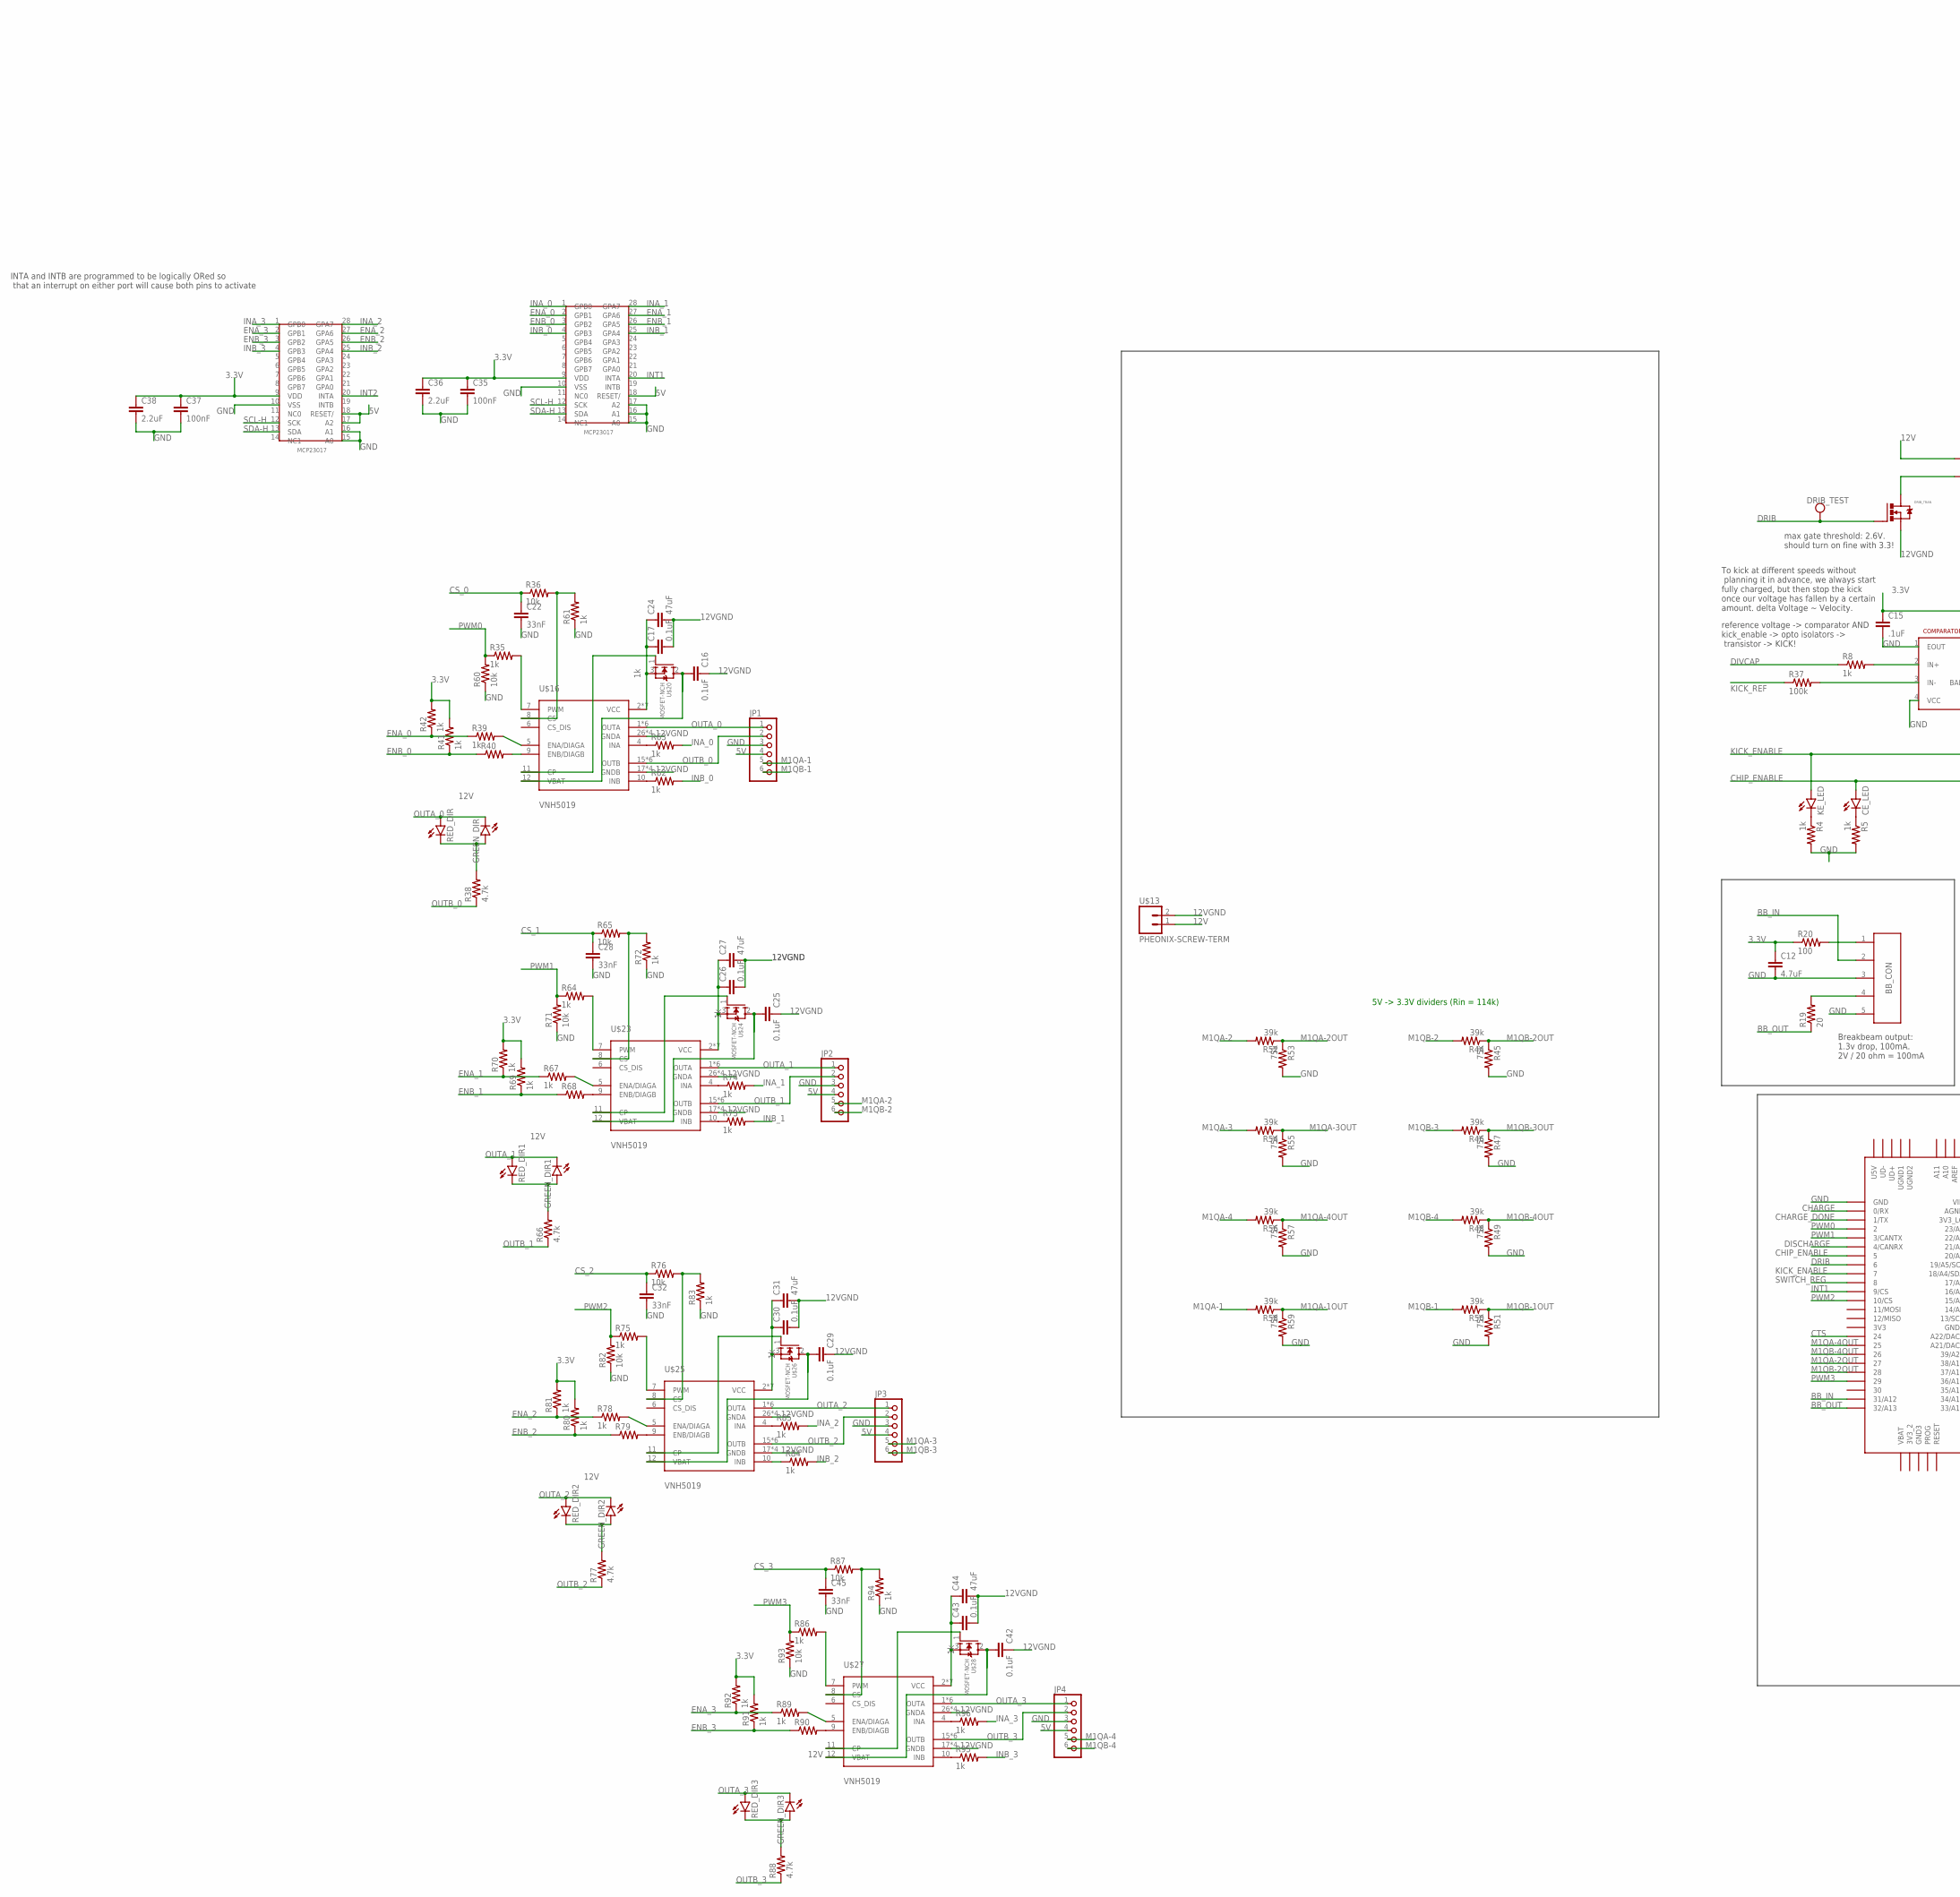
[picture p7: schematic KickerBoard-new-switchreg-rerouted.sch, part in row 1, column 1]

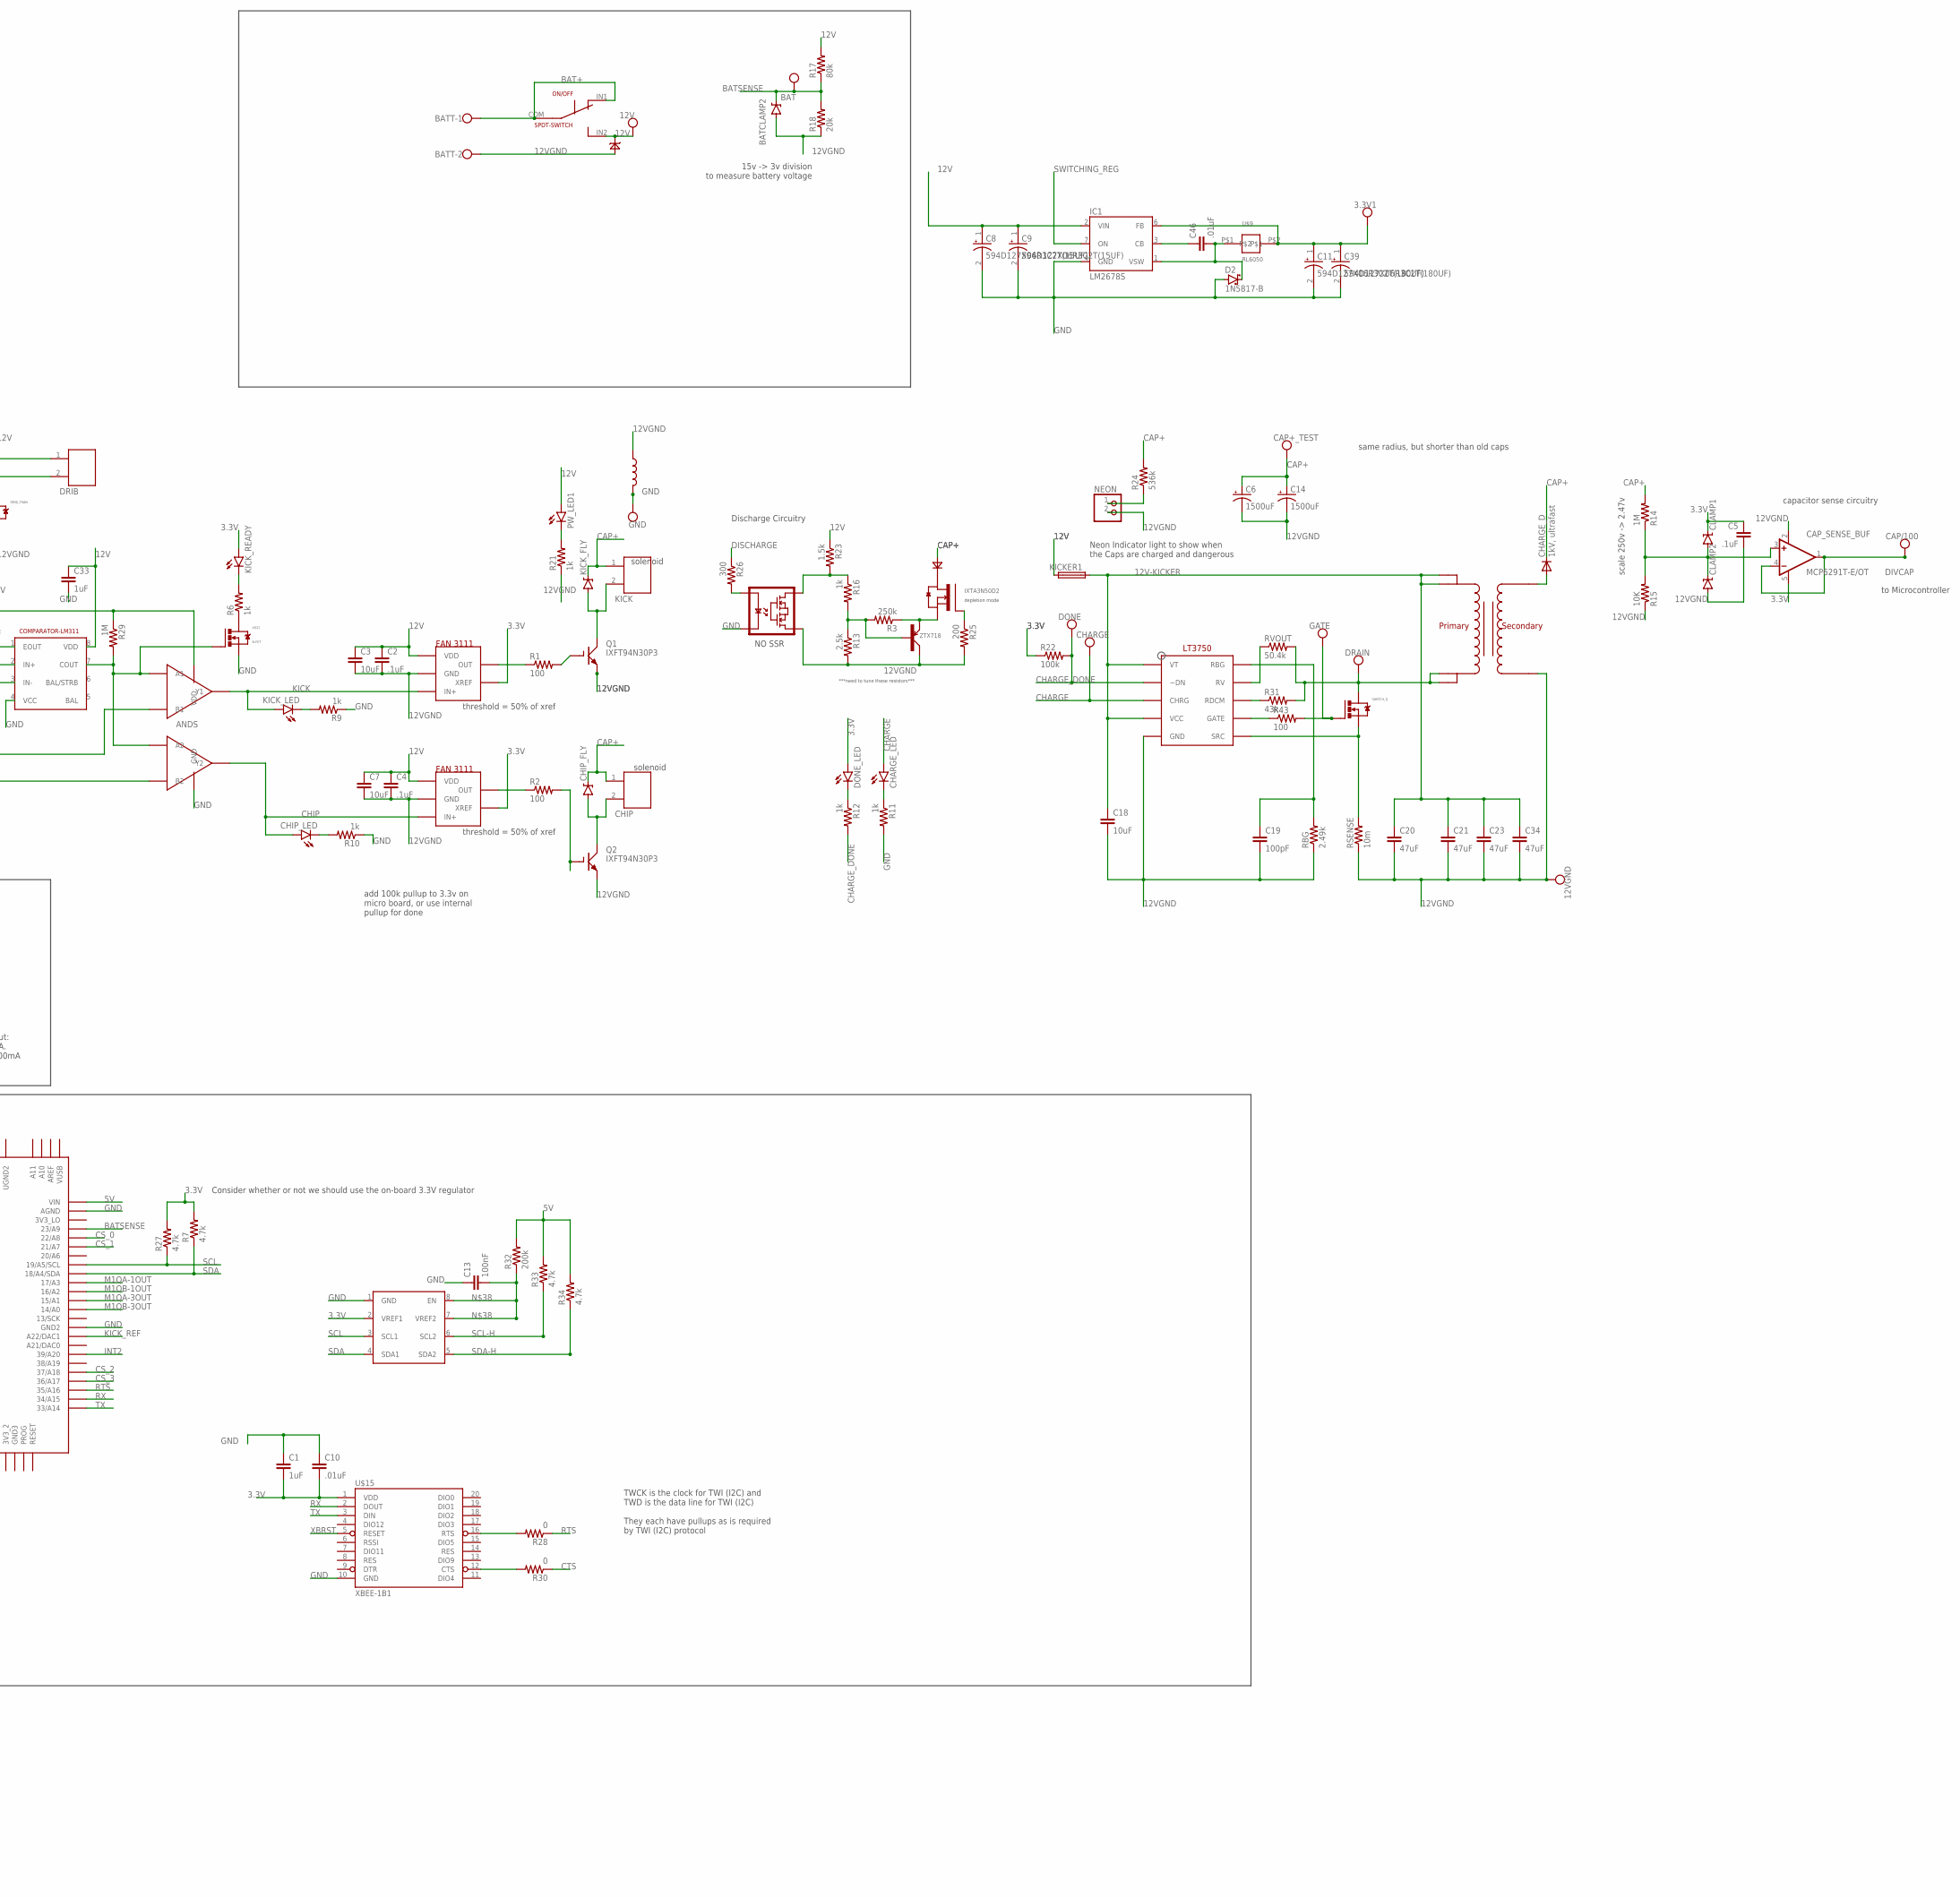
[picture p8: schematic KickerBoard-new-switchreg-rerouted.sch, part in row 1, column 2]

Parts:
3.3V1, 12V, 12VGND: TEST_PT; TESTING_PT
ANDS: AND-DUAL; TSSOP8
BAT: TEST_PT; TESTING_PT
BATCLAMP2: DIODE-ZENERDO214AC; DO214AC
BATT: W237-102
BB_CON: JST-5; JST-5-2MM
C1, C33: 1uF; 1206
C2, C4: .1uF; 1206
C3, C7: 10uF; 1206
C5, C15: .1uF; 0805
C6, C14: 1500uF; EB35D
C8, C9: 594D127X06R3C2T(15UF); CAPCP7132X250N
C10: .01uF; 1206
C11, C39: 594D127X06R3C2T(180UF); CAPCP7132X250N
C12: 4.7uF; 0805
C13, C35, C37: 100nF; 0805
C16, C17, C25, C26, C29, C30, C42, C43: 0.1uF; 0805
C18: 10uF; 0805
C19: 100pF; 0805
C20, C21, C23, C24, C27, C31, C34, C44: 47uF; 1206
C22, C28, C32, C45: 33nF; 0805
C36, C38: 2.2uF; 0805
C46: .01uF; 0805
CAP+_TEST: TEST_PT; TESTING_PT
CAP/100: TEST_PT; TESTING_PT
CAP_SENSE_BUF: MCP6291T-E/OT; SOT23-5
CE_LED: LED1206; LED-1206
CHARGE: TEST_PT; TESTING_PT
CHARGE_D: 1kV, ultrafast; DO214AC
CHARGE_LED: LED1206; LED-1206
CHARGE_U: LT3750; 10-MSOP
CHIP: JST-22MM; JST-2-2MM
CHIP_FLY: DIODE-ZENERDO214AB; DO214AB
CHIP_LED: LED1206; LED-1206
CLAMP1, CLAMP2: DIODE-ZENERDO214AC; DO214AC
D2: 1N5817-B; DO41-7.6
DONE: TEST_PT; TESTING_PT
DONE_LED: LED1206; LED-1206
DRAIN: TEST_PT; TESTING_PT
DRIB: JST-22MM; JST-2-2MM
DRIB_TEST: TEST_PT; TESTING_PT
DRIB_TRAN: N-MOSFETDPAK; DPAK
GATE: TEST_PT; TESTING_PT
GND: TEST_PT; TESTING_PT
GREEN_DIR, GREEN_DIR1, GREEN_DIR2, GREEN_DIR3: LED1206; LED-1206
IC1: LM2678S; TO263-7
JP1, JP2, JP3, JP4: PINHD-1X6; 1X06
KE_LED: LED1206; LED-1206
KICK: JST-22MM; JST-2-2MM
KICKER1: TR5
KICK_FLY: DIODE-ZENERDO214AB; DO214AB
KICK_LED: LED1206; LED-1206
KICK_READY: LED1206; LED-1206
NEON: PINHD-1X2; 1X02
ON/OFF: SPDT-SWITCH; CK_SWITCH
PW_LED1: LED1206; LED-1206
Q1, Q2: IXFT94N30P3; TO268
R1, R2, R20, R43: 100; 0805
R3: 250k; 0805
R4, R5, R6, R8, R9, R10, R11, R12, R16, R21, R35, R39, R40, R41, R42, R61, R62, R63, R64, R67, R68, R69, R70, R72, R73, R74, R75, R78, R79, R80, R81, R83, R84, R85, R86, R89, R90, R91, R92, R94, R95, R96: 1k; 0805
R7, R27, R33, R34, R38, R66, R77, R88: 4.7k; 0805
R13: 2.5k; 0805
R14, R29: 1M; 0805
R15: 10K; 0805
R17: 80k; 0805
R18: 20k; 0805
R19: 20; 0805
R22, R37: 100k; 0805
R23: 1.5k; 0805
R24: 536k; 0805
R25: 200; 0805
R26: 300; 0805
R28, R30: 0; 0805
R31: 43k; 0805
R32: 200k; 0805
R36, R60, R65, R71, R76, R82, R87, R93: 10k; 0805
R44, R46, R48, R50, R52, R54, R56, R58: 39k; 0805
R45, R47, R49, R51, R53, R55, R57, R59: 75k; 0805
RBG: 2.49k; 0805
RED_DIR, RED_DIR1, RED_DIR2, RED_DIR3: LED1206; LED-1206
RSENSE: 10m; R2512
RVOUT: 50.4k; 0805
SWITCH_Q: N-MOSFETDPAK; DPAK
U$1, U$4: FAN31111; SOT23-5
U$2: IXTA3N50D2; TO-263
U$3: 32052-TRANSFORMER; 10-TRANSFORMER
U$5: VO1400AEFTR; SOP4
U$6: ZTX718; TO92
U$7: 1N4007; THROUGH-HOLE-2
U$8: PCA9306; SOIC8
U$9: RL6050
U$12: 13VZENER; THROUGH-HOLE-2
U$13: PHEONIX-SCREW-TERM; 1X02-PHEONIX
U$14: TEENSY_3.5/3.6
U$15: XBEE-1B1; XBEE-1
U$16, U$23, U$25, U$27: VNH5019; MULTIPOWERSO-30
U$17, U$21: IO-EXPANDER; SSOP
U$18: LM311; SOIC8
U$19: INDUCTOR; 0805
U$20, U$24, U$26, U$28: MOSFET-NCH; TO252-3
U$22: N-FET; SOT-23

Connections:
3.3V: ANDS.P$8 (VDD), C1.2, C5.1, C10.2, C12.1, C15.1, C35.1, C36.1, C37.1, C38.1, CAP_SENSE_BUF.5 (V+), CLAMP1.C, DONE_LED.A, KICK_READY.A, R7.2, R20.1, R22.1, R27.2, R29.1, R41.2, R42.2, R69.2, R70.2, R80.2, R81.2, R91.2, R92.2, U$1.4 (XREF), U$4.4 (XREF), U$8.2 (VREF1), U$15.1 (VDD), U$17.9 (VDD), U$21.9 (VDD)
5V: JP1.4, JP2.4, JP3.4, JP4.4, R32.2, R33.2, R34.2, U$14.VIN, U$17.18 (RESET/), U$21.17 (A2), U$21.18 (RESET/)
12V: 12V.P$1, C2.1, C3.1, C4.1, C7.1, C8.1, C9.1, C16.1, C25.1, C29.1, C33.1, C42.1, DRIB.1, IC1.2 (VIN), KICKER1.1, ON/OFF.IN2 (P2), PW_LED1.A, R17.2, R23.1, U$1.1 (VDD), U$4.1 (VDD), U$12.-, U$13.1, U$16.12 (VBAT), U$18.8 (VDD), U$20.2 (D), U$23.12 (VBAT), U$24.2 (D), U$25.12 (VBAT), U$26.2 (D), U$27.12 (VBAT), U$28.2 (D)
12V-KICKER: C18.1, C20.1, C21.1, C23.1, C34.1, CHARGE_U.P$1 (VT), CHARGE_U.P$4 (VCC), KICKER1.2, U$3.P$4, U$3.P$5
12VGND: 12VGND.P$1, BATCLAMP2.A, BATT.2, C2.2, C3.2, C4.2, C5.2, C6.-, C7.2, C14.-, C16.2, C17.2, C18.2, C19.2, C20.2, C21.2, C23.2, C24.2, C25.2, C26.2, C27.2, C29.2, C30.2, C31.2, C34.2, C42.2, C43.2, C44.2, CAP_SENSE_BUF.2 (V-), CHARGE_U.P$5 (GND), CLAMP2.A, DRIB_TRAN.SOURCE (S), NEON.2, Q1.E, Q2.E, R13.2, R15.1, R18.1, R21.1, R25.2, RBG.1, RSENSE.1, U$1.2 (GND), U$3.P$10, U$4.2 (GND), U$5.3 (S2), U$6.LEFT (COLLECTOR), U$12.+, U$13.2, U$16.17 (GNDB), U$16.18 (GNDB), U$16.19 (GNDB), U$16.20 (GNDB), U$16.26 (GNDA), U$16.27 (GNDA), U$16.28 (GNDA), U$16.29 (GNDA), U$19.1, U$23.17 (GNDB), U$23.18 (GNDB), U$23.19 (GNDB), U$23.20 (GNDB), U$23.26 (GNDA), U$23.27 (GNDA), U$23.28 (GNDA), U$23.29 (GNDA), U$25.17 (GNDB), U$25.18 (GNDB), U$25.19 (GNDB), U$25.20 (GNDB), U$25.26 (GNDA), U$25.27 (GNDA), U$25.28 (GNDA), U$25.29 (GNDA), U$27.17 (GNDB), U$27.18 (GNDB), U$27.19 (GNDB), U$27.20 (GNDB), U$27.26 (GNDA), U$27.27 (GNDA), U$27.28 (GNDA), U$27.29 (GNDA)
BAT+: BATT.1, ON/OFF.COM, ON/OFF.IN1 (P1)
BATSENSE: BAT.P$1, BATCLAMP2.C, R17.1, R18.2, U$14.23/A9
BB_IN: BB_CON.2, U$14.31/A12
BB_OUT: R19.1, U$14.32/A13
CAP+: C6.+, C14.+, CAP+_TEST.P$1, CHARGE_D.C, CHIP.1, CHIP_FLY.CATHODE (C), KICK.1, KICK_FLY.CATHODE (C), R14.2, R24.2, U$7.+ (D+)
CHARGE: CHARGE.P$1, CHARGE_LED.A, CHARGE_U.P$3 (CHRG), U$14.0/RX
CHARGE_DONE: CHARGE_U.P$2 (~DN), DONE.P$1, R12.2, R22.2, U$14.1/TX
CHIP: ANDS.P$3 (Y2), CHIP_LED.A, U$1.3 (IN+)
CHIP_ENABLE: ANDS.P$6 (B2), CE_LED.A, U$14.5
COMP_OUT: ANDS.P$1 (A1), ANDS.P$5 (A2), R29.2, U$18.7 (COUT), U$22.G
CS_0: C22.1, R36.1, U$14.22/A8
CS_1: C28.1, R65.1, U$14.21/A7
CS_2: C32.1, R76.1, U$14.37/A18
CS_3: C45.1, R87.1, U$14.36/A17
CTS: R30.1, U$14.24
DISCHARGE: R26.1, U$14.4/CANRX
DIVCAP: CAP/100.P$1, CAP_SENSE_BUF.1 (OUT), CAP_SENSE_BUF.4 (-IN), R8.1
DRIB: DRIB_TEST.P$1, DRIB_TRAN.GATE (G), U$14.6
ENA_0: R39.1, R42.1, U$17.2 (GPB1)
ENA_1: R67.1, R70.1, U$17.27 (GPA6)
ENA_2: R78.1, R81.1, U$21.27 (GPA6)
ENA_3: R89.1, R92.1, U$21.2 (GPB1)
ENB_0: R40.1, R41.1, U$17.3 (GPB2)
ENB_1: R68.1, R69.1, U$17.26 (GPA5)
ENB_2: R79.1, R80.1, U$21.26 (GPA5)
ENB_3: R90.1, R91.1, U$21.3 (GPB2)
GND: ANDS.P$4 (GND), BB_CON.3, BB_CON.5, C1.1, C8.2, C9.2, C10.1, C11.2, C12.2, C13.1, C15.2, C22.2, C28.2, C32.2, C33.2, C35.2, C36.2, C37.2, C38.2, C39.2, C45.2, D2.A, GND.P$1, IC1.4 (GND), JP1.3, JP2.3, JP3.3, JP4.3, R4.2, R5.2, R9.1, R10.1, R11.2, R45.2, R47.2, R49.2, R51.2, R53.2, R55.2, R57.2, R59.2, R60.1, R61.1, R71.1, R72.1, R82.1, R83.1, R93.1, R94.1, U$5.2 (LED-), U$8.1 (GND), U$14.AGND, U$14.GND, U$14.GND2, U$15.10 (GND), U$17.10 (VSS), U$17.15 (A0), U$17.16 (A1), U$17.17 (A2), U$18.1 (EOUT), U$18.4 (VCC), U$19.2, U$21.10 (VSS), U$21.15 (A0), U$21.16 (A1), U$22.S
INA_0: R63.2, U$17.1 (GPB0)
INA_1: R74.2, U$17.28 (GPA7)
INA_2: R85.2, U$21.28 (GPA7)
INA_3: R96.2, U$21.1 (GPB0)
INB_0: R62.2, U$17.4 (GPB3)
INB_1: R73.2, U$17.25 (GPA4)
INB_2: R84.2, U$21.25 (GPA4)
INB_3: R95.2, U$21.4 (GPB3)
INT1: U$14.9/CS, U$17.20 (INTA)
INT2: U$14.39/A20, U$21.20 (INTA)
KICK: ANDS.P$7 (Y1), KICK_LED.A, U$4.3 (IN+)
KICK_ENABLE: ANDS.P$2 (B1), KE_LED.A, U$14.7
KICK_REF: R37.1, U$14.A22/DAC1
LOWCHIP: CHIP.2, CHIP_FLY.ANODE (A), Q2.C@1 (C), Q2.C@2 (C)
LOWKICK: KICK.2, KICK_FLY.ANODE (A), Q1.C@1 (C), Q1.C@2 (C)
M1QA-1: JP1.5, R58.2
M1QA-1OUT: R58.1, R59.1, U$14.17/A3
M1QA-2: JP2.5, R52.2
M1QA-2OUT: R52.1, R53.1, U$14.27
M1QA-3: JP3.5, R54.2
M1QA-3OUT: R54.1, R55.1, U$14.15/A1
M1QA-4: JP4.5, R56.2
M1QA-4OUT: R56.1, R57.1, U$14.25
M1QB-1: JP1.6, R50.2
M1QB-1OUT: R50.1, R51.1, U$14.16/A2
M1QB-2: JP2.6, R44.2
M1QB-2OUT: R44.1, R45.1, U$14.28
M1QB-3: JP3.6, R46.2
M1QB-3OUT: R46.1, R47.1, U$14.14/A0
M1QB-4: JP4.6, R48.2
M1QB-4OUT: R48.1, R49.1, U$14.26
unnamed: DRAIN.P$1, R31.2, RVOUT.2, SWITCH_Q.DRAIN (D), U$3.P$6, U$3.P$7
unnamed: R1.1, U$4.5 (OUT)
unnamed: Q2.G, R2.2
unnamed: R28.2, U$15.16 (RTS)
unnamed: R2.1, U$1.5 (OUT)
unnamed: CHARGE_U.P$8 (RDCM), R31.1
unnamed: C19.1, CHARGE_U.P$10 (RBG), RBG.2
unnamed: Q1.G, R1.2
unnamed: GATE.P$1, R43.2, SWITCH_Q.GATE (G)
unnamed: R3.1, U$2.LOWER_RIGHT (SOURCE), U$6.RIGHT (EMITTER)
unnamed: KE_LED.C, R4.1
unnamed: CHARGE_U.P$9 (RV), RVOUT.1
unnamed: CE_LED.C, R5.1
unnamed: R6.1, U$22.D
unnamed: KICK_LED.C, R9.2
unnamed: R30.2, U$15.12 (CTS)
unnamed: CHIP_LED.C, R10.2
unnamed: R3.2, R13.1, R16.2, U$6.CENTER (BASE)
unnamed: DONE_LED.C, R12.1
unnamed: CHARGE_LED.C, R11.1
unnamed: R25.1, U$2.LOWER_LEFT (GATE)
unnamed: PW_LED1.C, R21.2
unnamed: CHARGE_U.P$6 (SRC), RSENSE.2, SWITCH_Q.SOURCE (S)
unnamed: GREEN_DIR.A, R38.2, RED_DIR.C
unnamed: R36.2, R61.2, U$16.8 (CS)
unnamed: R35.2, U$16.7 (PWM)
unnamed: R39.2, U$16.5 (ENA/DIAGA)
unnamed: R16.1, R23.2, U$5.4 (S1)
unnamed: R26.2, U$5.1 (LED+)
unnamed: R40.2, U$16.9 (ENB/DIAGB)
unnamed: BB_CON.4, R19.2
unnamed: KICK_READY.C, R6.2
unnamed: CHARGE_U.P$7 (GATE), R43.1
unnamed: R8.2, U$18.2 (IN+)
unnamed: U$2.TAB (DRAIN), U$7.- (D-)
unnamed: R62.1, U$16.10 (INB)
unnamed: C13.2, R32.1, U$8.7 (VREF2), U$8.8 (EN)
unnamed: R63.1, U$16.4 (INA)
unnamed: BB_CON.1, R20.2
unnamed: U$16.11 (CP), U$20.1 (G)
unnamed: C17.1, C24.1, U$16.2 (VCC), U$16.3 (VCC), U$16.13 (VCC), U$16.14 (VCC), U$16.23 (VCC), U$16.VCC, U$16.VCC@1 (VCC), U$20.3 (S)
unnamed: GREEN_DIR1.A, R66.2, RED_DIR1.C
unnamed: R65.2, R72.2, U$23.8 (CS)
unnamed: R64.2, U$23.7 (PWM)
unnamed: R67.2, U$23.5 (ENA/DIAGA)
unnamed: R68.2, U$23.9 (ENB/DIAGB)
unnamed: U$23.11 (CP), U$24.1 (G)
unnamed: C26.1, C27.1, U$23.2 (VCC), U$23.3 (VCC), U$23.13 (VCC), U$23.14 (VCC), U$23.23 (VCC), U$23.VCC, U$23.VCC@1 (VCC), U$24.3 (S)
unnamed: R73.1, U$23.10 (INB)
unnamed: R74.1, U$23.4 (INA)
unnamed: GREEN_DIR2.A, R77.2, RED_DIR2.C
unnamed: R76.2, R83.2, U$25.8 (CS)
unnamed: R75.2, U$25.7 (PWM)
unnamed: R78.2, U$25.5 (ENA/DIAGA)
unnamed: R79.2, U$25.9 (ENB/DIAGB)
unnamed: U$25.11 (CP), U$26.1 (G)
unnamed: C30.1, C31.1, U$25.2 (VCC), U$25.3 (VCC), U$25.13 (VCC), U$25.14 (VCC), U$25.23 (VCC), U$25.VCC, U$25.VCC@1 (VCC), U$26.3 (S)
unnamed: R84.1, U$25.10 (INB)
unnamed: R85.1, U$25.4 (INA)
unnamed: GREEN_DIR3.A, R88.2, RED_DIR3.C
unnamed: R87.2, R94.2, U$27.8 (CS)
unnamed: R86.2, U$27.7 (PWM)
unnamed: R89.2, U$27.5 (ENA/DIAGA)
unnamed: R37.2, U$18.3 (IN-)
unnamed: R90.2, U$27.9 (ENB/DIAGB)
unnamed: U$27.11 (CP), U$28.1 (G)
unnamed: C43.1, C44.1, U$27.2 (VCC), U$27.3 (VCC), U$27.13 (VCC), U$27.14 (VCC), U$27.23 (VCC), U$27.VCC, U$27.VCC@1 (VCC), U$28.3 (S)
unnamed: R95.1, U$27.10 (INB)
unnamed: R96.1, U$27.4 (INA)
unnamed: C46.1, IC1.3 (CB)
unnamed: 3.3V1.P$1, C11.1, C39.1, IC1.6 (FB), U$9.P$2
unnamed: C46.2, D2.C, IC1.1 (VSW), U$9.P$1
OUTA_0: GREEN_DIR.C, JP1.1, RED_DIR.A, U$16.1 (OUTA), U$16.24 (OUTA), U$16.25 (OUTA), U$16.30 (OUTA), U$16.OUTA, U$16.OUTA@1 (OUTA)
OUTA_1: GREEN_DIR1.C, JP2.1, RED_DIR1.A, U$23.1 (OUTA), U$23.24 (OUTA), U$23.25 (OUTA), U$23.30 (OUTA), U$23.OUTA, U$23.OUTA@1 (OUTA)
OUTA_2: GREEN_DIR2.C, JP3.1, RED_DIR2.A, U$25.1 (OUTA), U$25.24 (OUTA), U$25.25 (OUTA), U$25.30 (OUTA), U$25.OUTA, U$25.OUTA@1 (OUTA)
OUTA_3: GREEN_DIR3.C, JP4.1, RED_DIR3.A, U$27.1 (OUTA), U$27.24 (OUTA), U$27.25 (OUTA), U$27.30 (OUTA), U$27.OUTA, U$27.OUTA@1 (OUTA)
OUTB_0: JP1.2, R38.1, U$16.15 (OUTB), U$16.16 (OUTB), U$16.21 (OUTB), U$16.22 (OUTB), U$16.OUTB, U$16.OUTB@1 (OUTB)
OUTB_1: JP2.2, R66.1, U$23.15 (OUTB), U$23.16 (OUTB), U$23.21 (OUTB), U$23.22 (OUTB), U$23.OUTB, U$23.OUTB@1 (OUTB)
OUTB_2: JP3.2, R77.1, U$25.15 (OUTB), U$25.16 (OUTB), U$25.21 (OUTB), U$25.22 (OUTB), U$25.OUTB, U$25.OUTB@1 (OUTB)
OUTB_3: JP4.2, R88.1, U$27.15 (OUTB), U$27.16 (OUTB), U$27.21 (OUTB), U$27.22 (OUTB), U$27.OUTB, U$27.OUTB@1 (OUTB)
PWM0: R35.1, R60.2, U$14.2
PWM1: R64.1, R71.2, U$14.3/CANTX
PWM2: R75.1, R82.2, U$14.10/CS
PWM3: R86.1, R93.2, U$14.29
RTS: R28.1, U$14.35/A16
RX: U$14.34/A15, U$15.2 (DOUT)
SCL: R27.1, U$8.3 (SCL1), U$14.19/A5/SCL
SCL-H: R33.1, U$8.6 (SCL2), U$17.12 (SCK), U$21.12 (SCK)
SDA: R7.1, U$8.4 (SDA1), U$14.18/A4/SDA
SDA-H: R34.1, U$8.5 (SDA2), U$17.13 (SDA), U$21.13 (SDA)
SWITCHING_REG: IC1.7 (ON)
SWITCH_REG: U$14.8
TO_DRIB: DRIB.2, DRIB_TRAN.DRAIN (D)
TO_NEON: NEON.1, R24.1
TRANS_OUT: CHARGE_D.A, U$3.P$1
TX: U$14.33/A14, U$15.3 (DIN)
UNBUF_DIVCAP: CAP_SENSE_BUF.3 (+IN), CLAMP1.A, CLAMP2.C, R14.1, R15.2
XBRST: U$15.5 (RESET)

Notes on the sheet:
scale 250v -> 2.47v
To kick at different speeds without planning it in advance, we always start fully charged, but then stop the kick once our voltage has fallen by a certain amount. delta Voltage ~ Velocity.
reference voltage -> comparator AND kick_enable -> opto isolators -> transistor -> KICK!
add 100k pullup to 3.3v on micro board, or use internal pullup for done
Neon Indicator light to show when the Caps are charged and dangerous
to Microcontroller
threshold = 50% of xref
same radius, but shorter than old caps
Discharge Circuitry
capacitor sense circuitry
15v -> 3v division to measure battery voltage
max gate threshold: 2.6V. should turn on fine with 3.3!
Breakbeam output: 1.3v drop, 100mA. 2V / 20 ohm = 100mA
solenoid
IXTA3N50D2
ZTX718
***need to tune these resistors***
depletion mode
NO SSR
TWCK is the clock for TWI (I2C) and TWD is the data line for TWI (I2C) They each have pullups as is required by TWI (I2C) protocol
INTA and INTB are programmed to be logically ORed so that an interrupt on either port will cause both pins to activate
5V -> 3.3V dividers (Rin = 114k)
Consider whether or not we should use the on-board 3.3V regulator

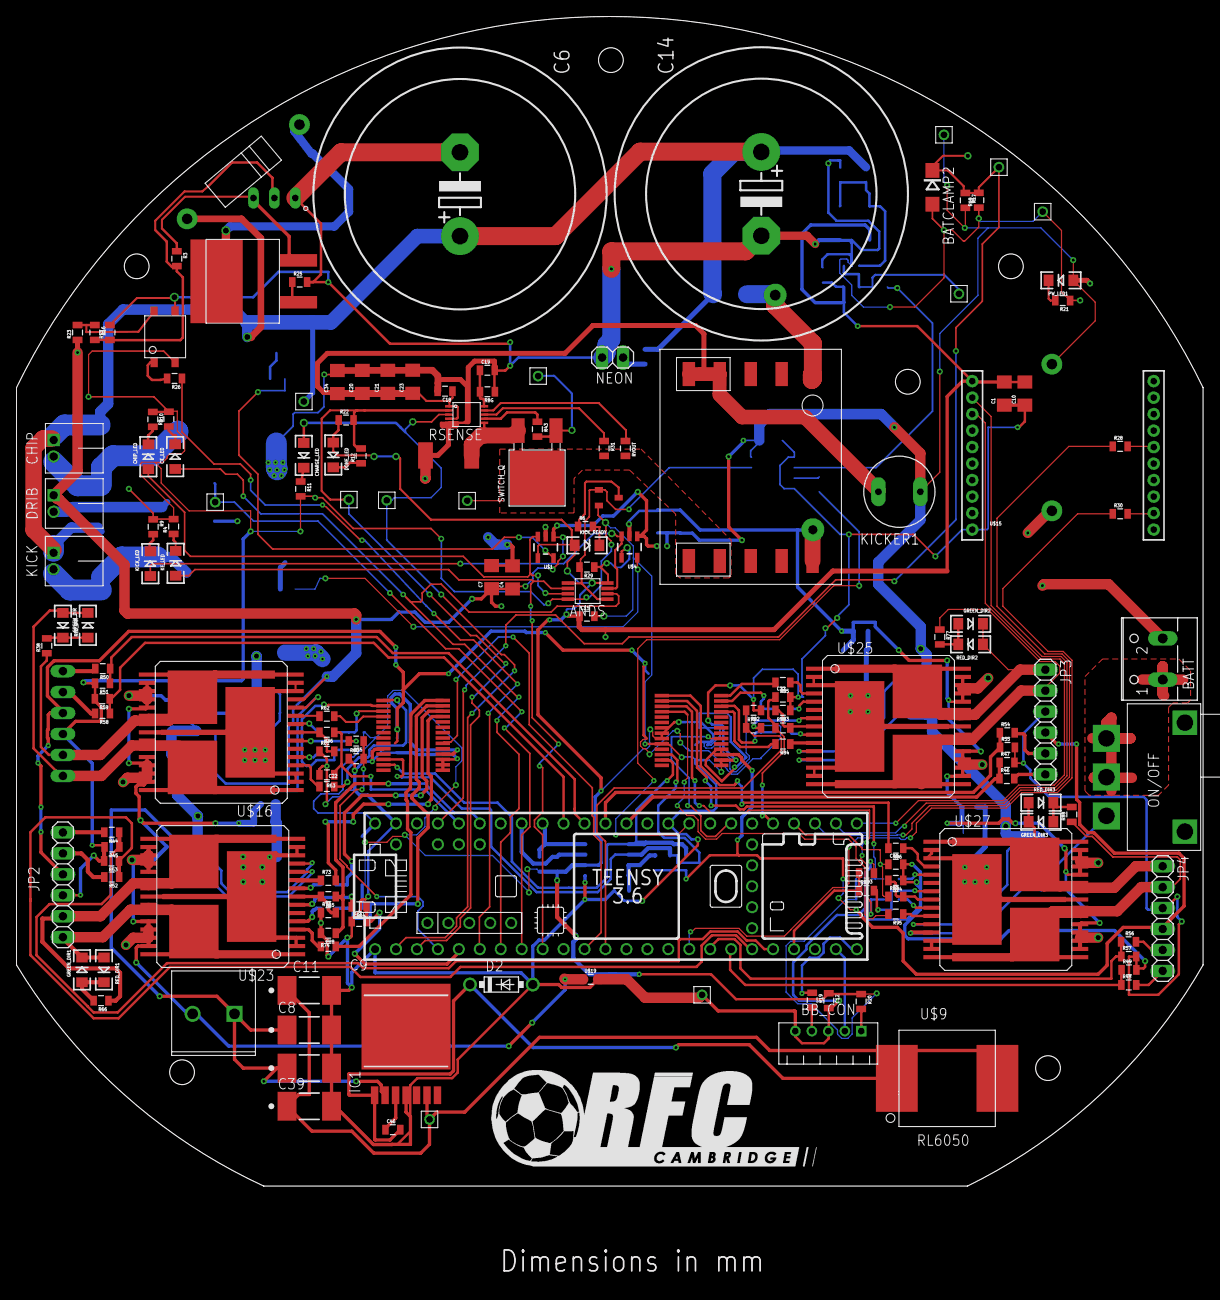
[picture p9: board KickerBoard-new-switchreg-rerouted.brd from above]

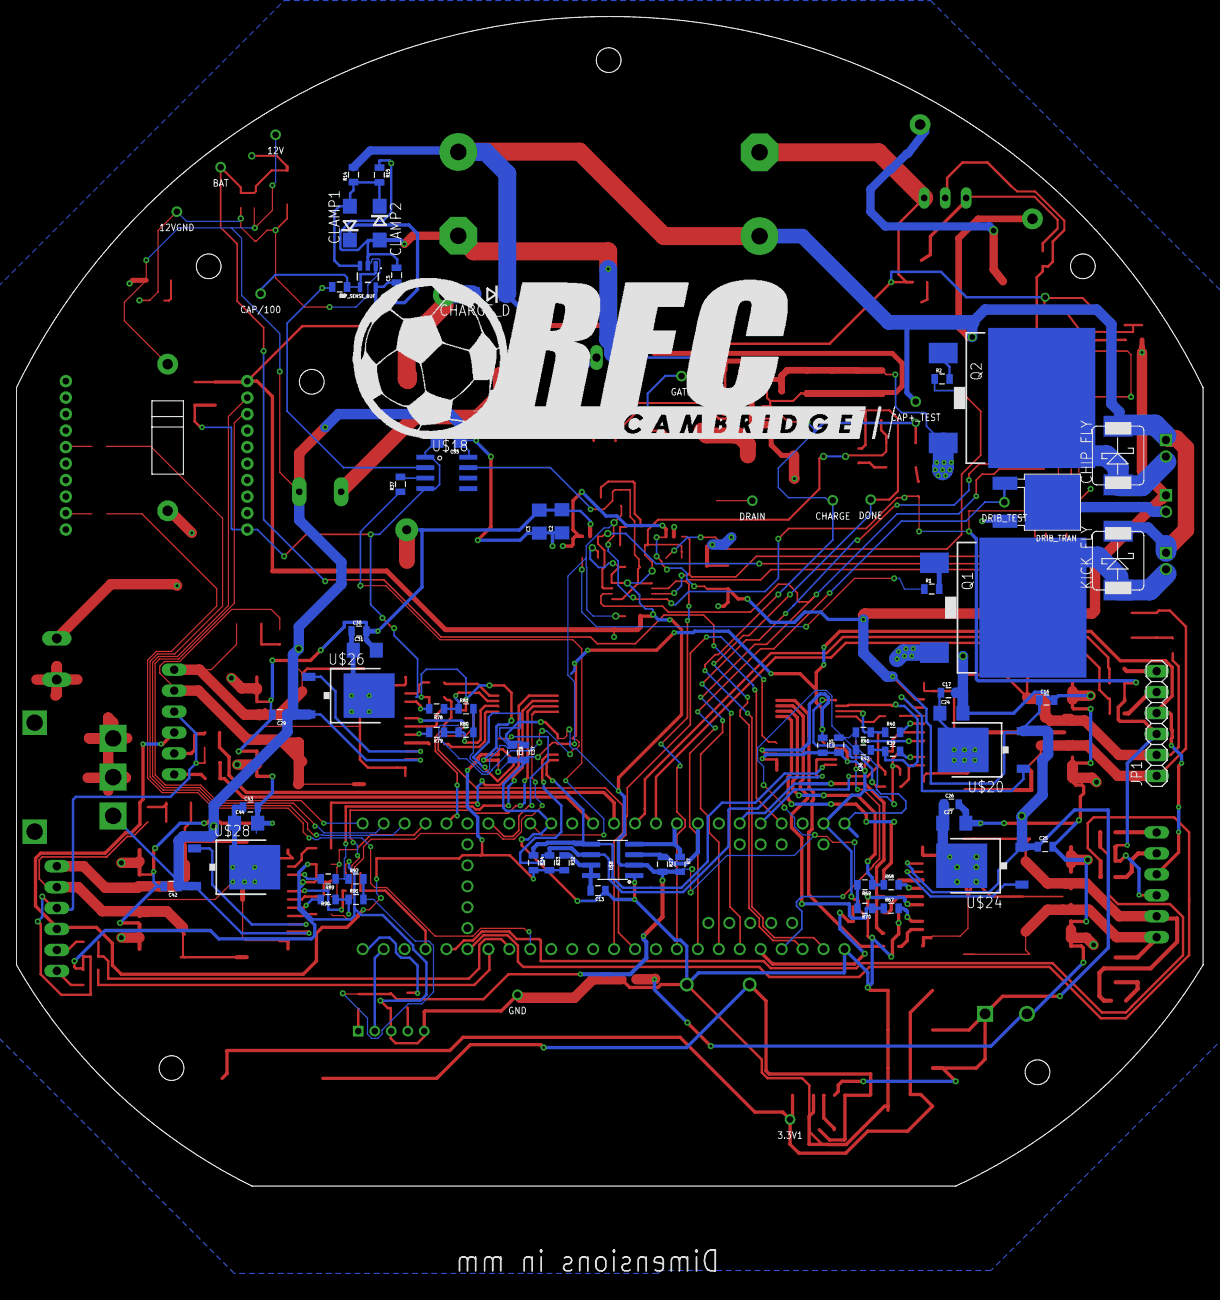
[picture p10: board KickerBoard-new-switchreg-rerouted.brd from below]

Board: 2 copper layers, 143.9 x 141.8 mm, 224 parts (66 on the bottom side), 158 nets.

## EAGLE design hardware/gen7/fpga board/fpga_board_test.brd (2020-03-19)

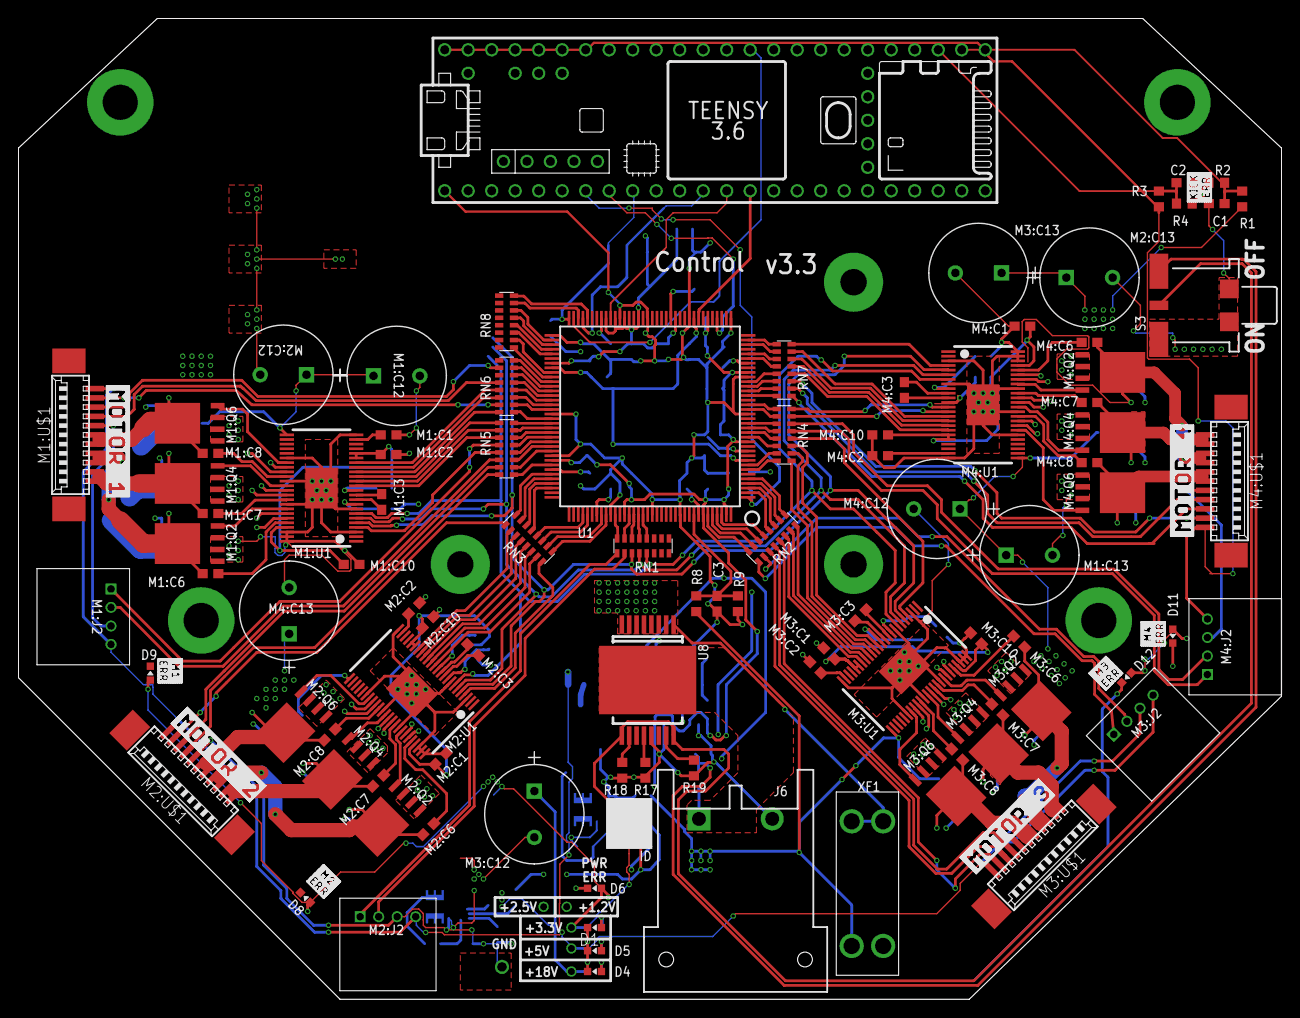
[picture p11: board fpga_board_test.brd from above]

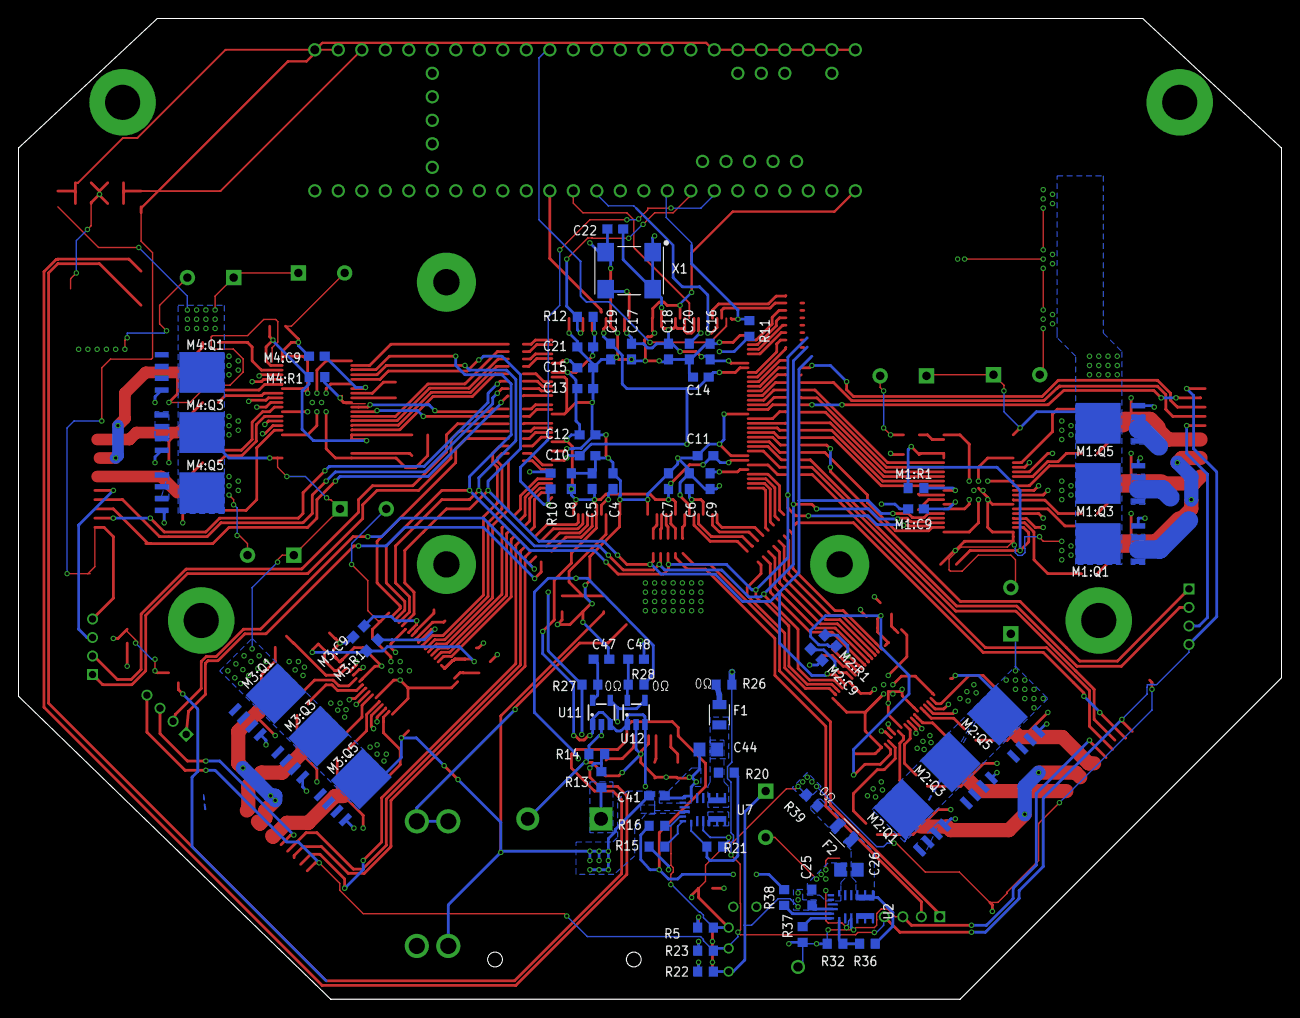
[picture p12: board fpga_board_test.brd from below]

Board: 6 copper layers, 136.5 x 106.0 mm, 175 parts (72 on the bottom side), 224 nets.

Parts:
C1: 0.1uF 50V; C0603
C2, C3, C4, C5, C6, C7, C8, C9, C10, C11, C12, C13, C14, C15, C16, C17, C18, C19, C20, C21, C22: 0.1uF; C0603
C25, C41: GRM188R6YA106MA73D; C0603
C26, C44: 22uF 16V; C0805
C47, C48: 1uF; C0603
D1, D4, D5: GREEN; CHIP-LED0603
D6, D8, D9, D11, D12: RED; CHIP-LED0603
F1, F2: 0805L200SLTHYR; FUSC2113X75
J6: DF22-2; DF22-2-H
M1:C1, M1:C2, M2:C1, M2:C2, M3:C1, M3:C2, M4:C1, M4:C2: 1uF; C0603
M1:C3, M2:C3, M3:C3, M4:C3: 0.022uF 50V; C0603
M1:C6, M1:C7, M1:C8, M1:C10, M2:C6, M2:C7, M2:C8, M2:C10, M3:C6, M3:C7, M3:C8, M3:C10, M4:C6, M4:C7, M4:C8, M4:C10: 0.1uF 50V; C0603
M1:C9, M2:C9, M3:C9, M4:C9: 2.2uF 50V; C0603
M1:C12, M1:C13, M2:C12, M2:C13, M3:C12, M3:C13, M4:C12, M4:C13: ECA-1HHG221; CAP_PAN_10X12.5
M1:J2, M2:J2, M3:J2, M4:J2: 4-PIN_2MM-H; 2MM-4-H
M1:Q1, M1:Q2, M1:Q3, M1:Q4, M1:Q5, M1:Q6, M2:Q1, M2:Q2, M2:Q3, M2:Q4, M2:Q5, M2:Q6, M3:Q1, M3:Q2, M3:Q3, M3:Q4, M3:Q5, M3:Q6, M4:Q1, M4:Q2, M4:Q3, M4:Q4, M4:Q5, M4:Q6: IRFH7545; PQFN_5X6_E
M1:R1, M2:R1, M3:R1, M4:R1: 10k; R0603
M1:U1, M2:U1, M3:U1, M4:U1: DRV8303DCA; TSSOP-48_PAD
M1:U$1, M2:U$1, M3:U$1, M4:U$1: MOTORCON; GEN3CON
R1: 68k 1%; R0603
R2, R3, R4: 10k 1%; R0603
R5, R18, R19, R22, R23: 1k; R0603
R8: 68k; R0603
R9, R17: 10k; R0603
R10, R12: 4.7k; R0603
R11: 330; R0603
R13: 270k; R0603
R14: 100k; R0603
R15: 43.2k; R0603
R16, R38: 150k; R0603
R20, R36: 160k 1%; R0603
R21: 30.1k 1%; R0603
R26, R27, R28, R39: 0; R0603
R32: 51.0k 1%; R0603
R37: 29.4k; R0603
RN1, RN2, RN3, RN4, RN5, RN6, RN7, RN8: 330; RA-8_2506
S3: 34EWMSP12M6RT
U1: XC3S250E-4TQG144C; TQFP144
U2, U7: MPM3620GQV-P
U8: VND5E006ASPTR-E; POWERSO-16
U11: MCP1824T-1202E/OT; SOT-23-5
U12: MCP1824T-2502E/OT; SOT-23-5
U$3: MOTOR-1
U$5: MOTOR-2
U$6: MOTOR-3
U$7: MOTOR-4
U$8: ERR-M1
U$10: TEENSY_3.5/3.6
U$12: ERR-M2
U$13: ERR-M3
U$14: ERR-M4
U$15: ERR-KICK
X1: ASV-18.432MHZ-EJ-T; ASV
XF1: 30A; 3557-2

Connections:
5V-LED: D5.A, R23.2
5V-LED1: D1.A, R5.2
18.5V-LED: D4.A, R22.1
!CS!-FPGA: U1.69, U$10.10/CS
+1.2V: C6.1, C10.1, C14.1, C19.1, R27.2, U1.9, U1.45, U1.80, U1.115
+1.2V-PRE: C47.1, R27.1, U11.5
+2.5V: C4.1, C9.1, C15.1, C20.1, R10.2, R11.2, R28.2, U1.30, U1.65, U1.102, U1.137
+2.5V-PRE: C48.1, R28.1, U12.5
+3.3V: C5.1, C7.1, C8.1, C11.1, C12.1, C13.1, C16.1, C17.1, C18.1, C21.1, C22.1, D6.A, D8.A, D9.A, D11.A, D12.A, R5.1, R12.1, R39.2, U1.13, U1.28, U1.42, U1.49, U1.57, U1.60, U1.62, U1.64, U1.79, U1.100, U1.121, U1.138, U1.143, U11.1, U11.3, U12.1, U12.3, X1.1, X1.4
+3.3V-FUSE: C26.1, F2.1, R36.2, U2.789
+5V: M1:J2.4, M1:U$1.1, M2:J2.4, M2:U$1.1, M3:J2.4, M3:U$1.1, M4:J2.4, M4:U$1.1, R3.1, R23.1, R26.2, U$10.VIN
+5V-FUSE: C44.1, F1.1, R20.2, U7.789
+18.5V: C25.1, C41.1, M1:C12.1, M1:C13.1, M1:Q1.5678, M1:Q3.5678, M1:Q5.5678, M1:U1.25, M2:C12.1, M2:C13.1, M2:Q1.5678, M2:Q3.5678, M2:Q5.5678, M2:U1.25, M3:C12.1, M3:C13.1, M3:Q1.5678, M3:Q3.5678, M3:Q5.5678, M3:U1.25, M4:C12.1, M4:C13.1, M4:Q1.5678, M4:Q3.5678, M4:Q5.5678, M4:U1.25, R1.1, R8.1, R22.2, U2.16, U7.16, XF1.3, XF1.4
AAM: R15.2, U7.18
AAM1: R37.2, U2.18
BATT-FPGA: C3.1, R8.2, R9.1, U1.136
CS1: R18.2, U8.10
CS2: R19.2, U8.15
CS-DIS: R17.2, U8.12
EN: R16.2, U7.17
EN1: R38.2, U2.17
EN-PWR: R16.1, R38.1, S3.2, U8.9, U8.16
EN-PWR-PRE: R13.1, R14.2, S3.1
FB: R20.1, R21.2, U7.1
FB1: R32.2, R36.1, U2.1
FPGA-CLK: U1.50, X1.3
FPGA-DONE: R11.1, U1.72, U$10.7
FPGA-INIT: R12.2, U1.40, U$10.6
FPGA-PROG: R10.1, U1.1, U$10.5
GND: C1.2, C2.2, C3.2, C4.2, C5.2, C6.2, C7.2, C8.2, C9.2, C10.2, C11.2, C12.2, C13.2, C14.2, C15.2, C16.2, C17.2, C18.2, C19.2, C20.2, C21.2, C22.2, C25.2, C26.2, C41.2, C44.2, C47.2, C48.2, D1.C, D4.C, D5.C, J6.2, M1:C1.2, M1:C2.2, M1:C9.2, M1:C10.2, M1:C12.2, M1:C13.2, M1:J2.3, M1:Q2.1, M1:Q2.2, M1:Q2.3, M1:Q4.1, M1:Q4.2, M1:Q4.3, M1:Q6.1, M1:Q6.2, M1:Q6.3, M1:U1.3, M1:U1.8, M1:U1.24, M1:U1.30, M1:U1.35, M1:U1.40, M1:U1.46, M1:U1.47, M1:U1.48, M1:U1.PAD, M1:U$1.5, M2:C1.2, M2:C2.2, M2:C9.2, M2:C10.2, M2:C12.2, M2:C13.2, M2:J2.3, M2:Q2.1, M2:Q2.2, M2:Q2.3, M2:Q4.1, M2:Q4.2, M2:Q4.3, M2:Q6.1, M2:Q6.2, M2:Q6.3, M2:U1.3, M2:U1.8, M2:U1.24, M2:U1.30, M2:U1.35, M2:U1.40, M2:U1.46, M2:U1.47, M2:U1.48, M2:U1.PAD, M2:U$1.5, M3:C1.2, M3:C2.2, M3:C9.2, M3:C10.2, M3:C12.2, M3:C13.2, M3:J2.3, M3:Q2.1, M3:Q2.2, M3:Q2.3, M3:Q4.1, M3:Q4.2, M3:Q4.3, M3:Q6.1, M3:Q6.2, M3:Q6.3, M3:U1.3, M3:U1.8, M3:U1.24, M3:U1.30, M3:U1.35, M3:U1.40, M3:U1.46, M3:U1.47, M3:U1.48, M3:U1.PAD, M3:U$1.5, M4:C1.2, M4:C2.2, M4:C9.2, M4:C10.2, M4:C12.2, M4:C13.2, M4:J2.3, M4:Q2.1, M4:Q2.2, M4:Q2.3, M4:Q4.1, M4:Q4.2, M4:Q4.3, M4:Q6.1, M4:Q6.2, M4:Q6.3, M4:U1.3, M4:U1.8, M4:U1.24, M4:U1.30, M4:U1.35, M4:U1.40, M4:U1.46, M4:U1.47, M4:U1.48, M4:U1.PAD, M4:U$1.5, R2.2, R4.2, R9.2, R14.1, R15.1, R17.1, R18.1, R19.1, R21.1, R32.1, R37.1, S3.3, S3.LEG1, S3.LEG3, U1.11, U1.19, U1.27, U1.37, U1.46, U1.55, U1.61, U1.73, U1.90, U1.99, U1.118, U1.127, U1.133, U2.3, U2.12, U2.13, U2.14, U7.3, U7.12, U7.13, U7.14, U8.13, U11.2, U12.2, U$10.GND, X1.2
M1-!CS: M1:U1.4, RN5.13
M1-A-H: M1:U1.15, RN5.9
M1-A-L: M1:U1.16, RN6.16
M1-B-H: M1:U1.13, RN5.11
M1-B-L: M1:U1.14, RN5.10
M1-C-H: M1:U1.17, RN6.14
M1-C-L: M1:U1.18, RN6.13
M1-ENC-A: M1:J2.2, RN5.14
M1-ENC-B: M1:J2.1, RN5.12
M1-H1: M1:U$1.3, RN6.10
M1-H2: M1:U$1.4, RN6.12
M1-H3: M1:U$1.2, RN6.15
M1:+3.3V: M1:C1.1, M1:C10.1, M1:R1.1, M1:U1.19, M1:U1.20, M1:U1.45
M1:AVDD: M1:C2.1, M1:U1.23
M1:BST-A: M1:C6.1, M1:U1.44
M1:BST-B: M1:C7.1, M1:U1.39
M1:BST-C: M1:C8.1, M1:U1.34
M1:CP1: M1:C3.1, M1:U1.10
M1:CP2: M1:C3.2, M1:U1.11
M1:EN-GATE: M1:R1.2, M1:U1.12
M1:GH-A: M1:Q1.4, M1:U1.43
M1:GH-B: M1:Q3.4, M1:U1.38
M1:GH-C: M1:Q5.4, M1:U1.33
M1:GL-A: M1:Q2.4, M1:U1.41
M1:GL-B: M1:Q4.4, M1:U1.36
M1:GL-C: M1:Q6.4, M1:U1.31
M1:GVDD: M1:C9.1, M1:U1.9
M1:PHASE-A: M1:C7.2, M1:Q3.1, M1:Q3.2, M1:Q3.3, M1:Q4.5678, M1:U1.37, M1:U$1.10, M1:U$1.11
M1:PHASE-B: M1:C6.2, M1:Q1.1, M1:Q1.2, M1:Q1.3, M1:Q2.5678, M1:U1.42, M1:U$1.8, M1:U$1.9
M1:PHASE-C: M1:C8.2, M1:Q5.1, M1:Q5.2, M1:Q5.3, M1:Q6.5678, M1:U1.32, M1:U$1.6, M1:U$1.7
M2-!CS: M2:U1.4, RN3.16
M2-A-H: M2:U1.15, RN3.13
M2-A-L: M2:U1.16, RN3.12
M2-B-H: M2:U1.13, RN3.15
M2-B-L: M2:U1.14, RN3.14
M2-C-H: M2:U1.17, RN3.11
M2-C-L: M2:U1.18, RN3.10
M2-ENC-A: M2:J2.2, RN1.10
M2-ENC-B: M2:J2.1, RN1.9
M2-H1: M2:U$1.3, RN5.15
M2-H2: M2:U$1.4, RN5.16
M2-H3: M2:U$1.2, RN3.9
M2:+3.3V: M2:C1.1, M2:C10.1, M2:R1.1, M2:U1.19, M2:U1.20, M2:U1.45
M2:AVDD: M2:C2.1, M2:U1.23
M2:BST-A: M2:C6.1, M2:U1.44
M2:BST-B: M2:C7.1, M2:U1.39
M2:BST-C: M2:C8.1, M2:U1.34
M2:CP1: M2:C3.1, M2:U1.10
M2:CP2: M2:C3.2, M2:U1.11
M2:EN-GATE: M2:R1.2, M2:U1.12
M2:GH-A: M2:Q1.4, M2:U1.43
M2:GH-B: M2:Q3.4, M2:U1.38
M2:GH-C: M2:Q5.4, M2:U1.33
M2:GL-A: M2:Q2.4, M2:U1.41
M2:GL-B: M2:Q4.4, M2:U1.36
M2:GL-C: M2:Q6.4, M2:U1.31
M2:GVDD: M2:C9.1, M2:U1.9
M2:PHASE-A: M2:C7.2, M2:Q3.1, M2:Q3.2, M2:Q3.3, M2:Q4.5678, M2:U1.37, M2:U$1.10, M2:U$1.11
M2:PHASE-B: M2:C6.2, M2:Q1.1, M2:Q1.2, M2:Q1.3, M2:Q2.5678, M2:U1.42, M2:U$1.8, M2:U$1.9
M2:PHASE-C: M2:C8.2, M2:Q5.1, M2:Q5.2, M2:Q5.3, M2:Q6.5678, M2:U1.32, M2:U$1.6, M2:U$1.7
M3-!CS: M3:U1.4, RN4.12
M3-A-H: M3:U1.15, RN4.9
M3-A-L: M3:U1.16, RN2.16
M3-B-H: M3:U1.13, RN4.11
M3-B-L: M3:U1.14, RN4.10
M3-C-H: M3:U1.17, RN2.15
M3-C-L: M3:U1.18, RN2.14
M3-ENC-A: M3:J2.2, RN2.10
M3-ENC-B: M3:J2.1, RN2.9
M3-H1: M3:U$1.3, RN2.11
M3-H2: M3:U$1.4, RN2.12
M3-H3: M3:U$1.2, RN2.13
M3:+3.3V: M3:C1.1, M3:C10.1, M3:R1.1, M3:U1.19, M3:U1.20, M3:U1.45
M3:AVDD: M3:C2.1, M3:U1.23
M3:BST-A: M3:C6.1, M3:U1.44
M3:BST-B: M3:C7.1, M3:U1.39
M3:BST-C: M3:C8.1, M3:U1.34
M3:CP1: M3:C3.1, M3:U1.10
M3:CP2: M3:C3.2, M3:U1.11
M3:EN-GATE: M3:R1.2, M3:U1.12
M3:GH-A: M3:Q1.4, M3:U1.43
M3:GH-B: M3:Q3.4, M3:U1.38
M3:GH-C: M3:Q5.4, M3:U1.33
M3:GL-A: M3:Q2.4, M3:U1.41
M3:GL-B: M3:Q4.4, M3:U1.36
M3:GL-C: M3:Q6.4, M3:U1.31
M3:GVDD: M3:C9.1, M3:U1.9
M3:PHASE-A: M3:C7.2, M3:Q3.1, M3:Q3.2, M3:Q3.3, M3:Q4.5678, M3:U1.37, M3:U$1.10, M3:U$1.11
M3:PHASE-B: M3:C6.2, M3:Q1.1, M3:Q1.2, M3:Q1.3, M3:Q2.5678, M3:U1.42, M3:U$1.8, M3:U$1.9
M3:PHASE-C: M3:C8.2, M3:Q5.1, M3:Q5.2, M3:Q5.3, M3:Q6.5678, M3:U1.32, M3:U$1.6, M3:U$1.7
M4-!CS: M4:U1.4, RN7.16
M4-A-H: M4:U1.15, RN7.15
M4-A-L: M4:U1.16, RN7.14
M4-B-H: M4:U1.13, RN4.16
M4-B-L: M4:U1.14, RN4.15
M4-C-H: M4:U1.17, RN7.13
M4-C-L: M4:U1.18, RN7.12
M4-ENC-A: M4:J2.2, RN4.14
M4-ENC-B: M4:J2.1, RN4.13
M4-H1: M4:U$1.3, RN7.9
M4-H2: M4:U$1.4, RN7.10
M4-H3: M4:U$1.2, RN7.11
M4:+3.3V: M4:C1.1, M4:C10.1, M4:R1.1, M4:U1.19, M4:U1.20, M4:U1.45
M4:AVDD: M4:C2.1, M4:U1.23
M4:BST-A: M4:C6.1, M4:U1.44
M4:BST-B: M4:C7.1, M4:U1.39
M4:BST-C: M4:C8.1, M4:U1.34
M4:CP1: M4:C3.1, M4:U1.10
M4:CP2: M4:C3.2, M4:U1.11
M4:EN-GATE: M4:R1.2, M4:U1.12
M4:GH-A: M4:Q1.4, M4:U1.43
M4:GH-B: M4:Q3.4, M4:U1.38
M4:GH-C: M4:Q5.4, M4:U1.33
M4:GL-A: M4:Q2.4, M4:U1.41
M4:GL-B: M4:Q4.4, M4:U1.36
M4:GL-C: M4:Q6.4, M4:U1.31
M4:GVDD: M4:C9.1, M4:U1.9
M4:PHASE-A: M4:C7.2, M4:Q3.1, M4:Q3.2, M4:Q3.3, M4:Q4.5678, M4:U1.37, M4:U$1.10, M4:U$1.11
M4:PHASE-B: M4:C6.2, M4:Q1.1, M4:Q1.2, M4:Q1.3, M4:Q2.5678, M4:U1.42, M4:U$1.8, M4:U$1.9
M4:PHASE-C: M4:C8.2, M4:Q5.1, M4:Q5.2, M4:Q5.3, M4:Q6.5678, M4:U1.32, M4:U$1.6, M4:U$1.7
MISO-AUX: M1:U1.6, M2:U1.6, M3:U1.6, M4:U1.6, RN1.12
MISO-FPGA: U1.44, U$10.12/MISO
MOSI-AUX: M1:U1.5, M2:U1.5, M3:U1.5, M4:U1.5, RN1.11
MOSI-FPGA: U1.63, U$10.11/MOSI
unnamed: F2.2, R39.1
unnamed: F1.2, R26.1
PWR-ERR: D6.C, U11.4, U12.4
R-P1: RN8.1, U1.82
R-P2: RN8.2, U1.81
R-P3: RN8.3, U1.77
R-P4: RN8.4, U1.76
R-P5: RN8.5, U1.75
R-P6: RN8.6, U1.74
R-P7: RN8.7, U1.70
R-P8: RN8.8, U1.68
R-P9: RN6.1, U1.91
R-P10: RN6.2, U1.89
R-P11: RN6.3, U1.88
R-P12: RN6.4, U1.87
R-P13: RN6.5, U1.86
R-P14: RN6.6, U1.85
R-P15: RN6.7, U1.84
R-P16: RN6.8, U1.83
R-P17: RN5.1, U1.101
R-P18: RN5.2, U1.98
R-P19: RN5.3, U1.97
R-P20: RN5.4, U1.96
R-P21: RN5.5, U1.95
R-P22: RN5.6, U1.94
R-P23: RN5.7, U1.93
R-P24: RN5.8, U1.92
R-P25: RN3.1, U1.117
R-P26: RN3.2, U1.116
R-P27: RN3.3, U1.113
R-P28: RN3.4, U1.112
R-P29: RN3.5, U1.106
R-P30: RN3.6, U1.105
R-P31: RN3.7, U1.104
R-P32: RN3.8, U1.103
R-P36: RN1.4, U1.125
R-P37: RN1.5, U1.124
R-P38: RN1.6, U1.123
R-P39: RN1.7, U1.122
R-P40: RN1.8, U1.119
R-P41: RN2.1, U1.5
R-P42: RN2.2, U1.4
R-P43: RN2.3, U1.3
R-P44: RN2.4, U1.2
R-P45: RN2.5, U1.142
R-P46: RN2.6, U1.141
R-P47: RN2.7, U1.140
R-P48: RN2.8, U1.139
R-P49: RN4.1, U1.21
R-P50: RN4.2, U1.20
R-P51: RN4.3, U1.17
R-P52: RN4.4, U1.16
R-P53: RN4.5, U1.15
R-P54: RN4.6, U1.14
R-P55: RN4.7, U1.8
R-P56: RN4.8, U1.7
R-P57: RN7.1, U1.35
R-P58: RN7.2, U1.34
R-P59: RN7.3, U1.32
R-P60: RN7.4, U1.31
R-P61: RN7.5, U1.26
R-P62: RN7.6, U1.25
R-P63: RN7.7, U1.24
R-P64: RN7.8, U1.23
SCK-AUX: M1:U1.7, M2:U1.7, M3:U1.7, M4:U1.7, RN1.13
SCK-FPGA: U1.71, U$10.13/SCK
SENSE-BATT: C1.1, R1.2, R2.1, U$10.34/A15
SENSE-VIN: C2.1, R3.2, R4.1, U$10.35/A16
VBATT: U8.1, U8.2, U8.3, U8.4, U8.5, U8.6, U8.7, U8.8, XF1.1, XF1.2
VIN: J6.1, R13.2, U8.17

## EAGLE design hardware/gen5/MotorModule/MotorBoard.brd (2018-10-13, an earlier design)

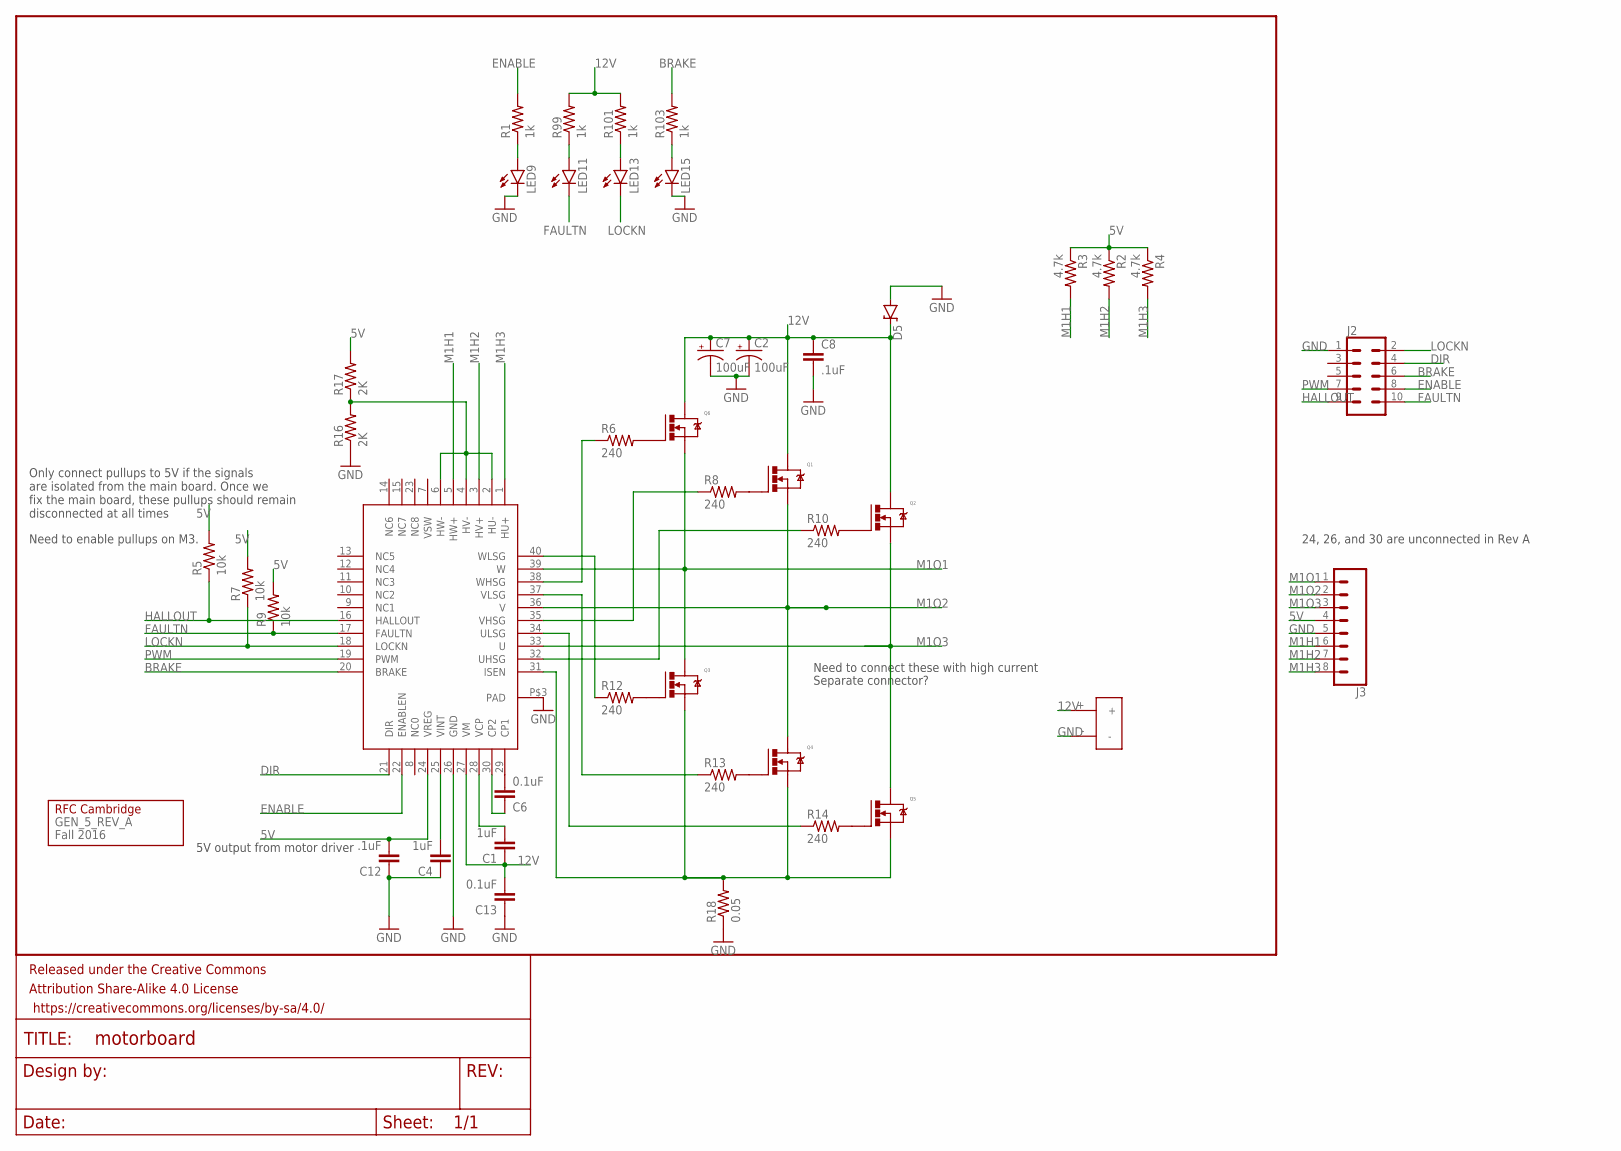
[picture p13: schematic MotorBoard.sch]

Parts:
C1, C4: 1uF; 0805
C2, C7: 100uF; PANASONIC_D
C6, C13: 0.1uF; 0805
C8, C12: .1uF; 0805
D5: DIODE-ZENERDO214AC; DO214AC
FRAME7: FRAME-LETTER; CREATIVE_COMMONS
GEN_5_REV_A: Fall 2016; LOGO
J2: CONN_05X2SHD; 2X5-SHROUDED
J3: CONN_08LONGPADS; 1X08_LONGPADS
LED9, LED11, LED13, LED15: LED1206; LED-1206
Q1, Q2, Q3, Q4, Q5, Q6: N-MOSFET; DPAK
R1, R99, R101, R103: 1k; 0805
R2, R3, R4: 4.7k; 0805
R5, R7, R9: 10k; 0805
R6, R8, R10, R12, R13, R14: 240; 0805
R16, R17: 2K; 0805
R18: 0.05; R2512
U$1: DRV8307; QFN40-6X6
U$2: POWER_CONN_2X1

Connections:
5V: C12.2, J3.4, R2.1, R3.1, R4.1, R5.2, R7.2, R9.2, R17.2, U$1.24 (VREG)
12V: C1.1, C2.+, C7.+, C8.1, C13.2, D5.C, Q1.DRAIN, Q2.DRAIN, Q6.DRAIN, R99.2, R101.2, U$1.27 (VM), U$2.+
BRAKE: J2.6, R103.2, U$1.20 (BRAKE)
DIR: J2.4, U$1.21 (DIR)
ENABLE: J2.8, R1.2, U$1.22 (ENABLEN)
FAULTN: J2.10, LED11.C, R9.1, U$1.17 (FAULTN)
GND: C2.-, C4.1, C7.-, C8.2, C12.1, C13.1, D5.A, J2.1, J3.5, LED9.C, LED15.C, R16.1, R18.1, U$1.26 (GND), U$1.P$3 (PAD), U$2.-
HALLOUT: J2.9, R5.1, U$1.16 (HALLOUT)
LOCKN: J2.2, LED13.C, R7.1, U$1.18 (LOCKN)
M1H1: J3.6, R3.2, U$1.5 (HW+)
M1H2: J3.7, R2.2, U$1.3 (HV+)
M1H3: J3.8, R4.2, U$1.1 (HU+)
M1O1: J3.1, Q3.DRAIN, Q6.SOURCE, U$1.39 (W)
M1O2: J3.2, Q1.SOURCE, Q4.DRAIN, U$1.36 (V)
M1O3: J3.3, Q2.SOURCE, Q5.DRAIN, U$1.33 (U)
unnamed: LED9.A, R1.1
unnamed: C6.2, U$1.29 (CP1)
unnamed: C1.2, U$1.28 (VCP)
unnamed: Q6.GATE, R6.2
unnamed: Q1.GATE, R8.2
unnamed: C6.1, U$1.30 (CP2)
unnamed: Q2.GATE, R10.2
unnamed: Q3.GATE, R12.2
unnamed: Q4.GATE, R13.2
unnamed: Q5.GATE, R14.2
unnamed: C4.2, U$1.25 (VINT)
unnamed: R6.1, U$1.38 (WHSG)
unnamed: R14.1, U$1.34 (ULSG)
unnamed: R13.1, U$1.37 (VLSG)
unnamed: R12.1, U$1.40 (WLSG)
unnamed: R8.1, U$1.35 (VHSG)
unnamed: R10.1, U$1.32 (UHSG)
unnamed: R16.2, R17.1, U$1.2 (HU-), U$1.4 (HV-), U$1.6 (HW-)
unnamed: LED11.A, R99.1
unnamed: LED13.A, R101.1
unnamed: LED15.A, R103.1
O1: Q3.SOURCE, Q4.SOURCE, Q5.SOURCE, R18.2, U$1.31 (ISEN)
PWM: J2.7, U$1.19 (PWM)

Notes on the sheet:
5V output from motor driver
Need to connect these with high current
Separate connector?
24, 26, and 30 are unconnected in Rev A
Need to enable pullups on M3.
Only connect pullups to 5V if the signals are isolated from the main board. Once we fix the main board, these pullups should remain disconnected at all times

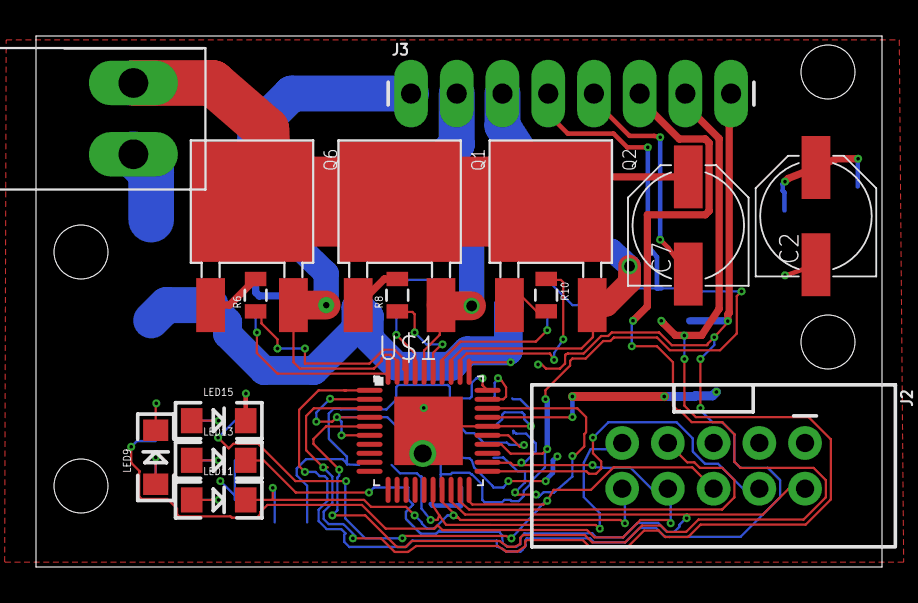
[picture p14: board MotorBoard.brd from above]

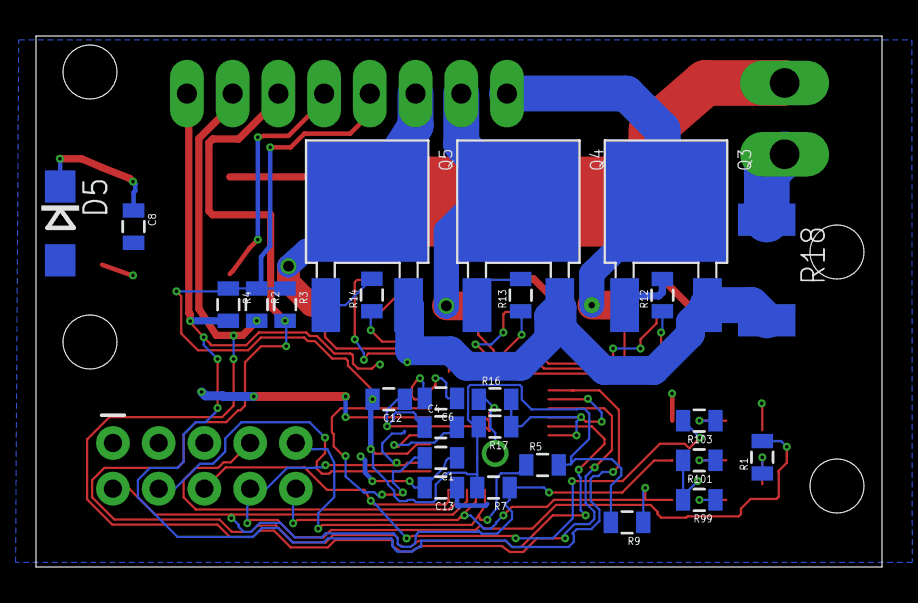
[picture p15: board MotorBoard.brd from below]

Board: 2 copper layers, 47.0 x 29.5 mm, 44 parts (26 on the bottom side), 38 nets.

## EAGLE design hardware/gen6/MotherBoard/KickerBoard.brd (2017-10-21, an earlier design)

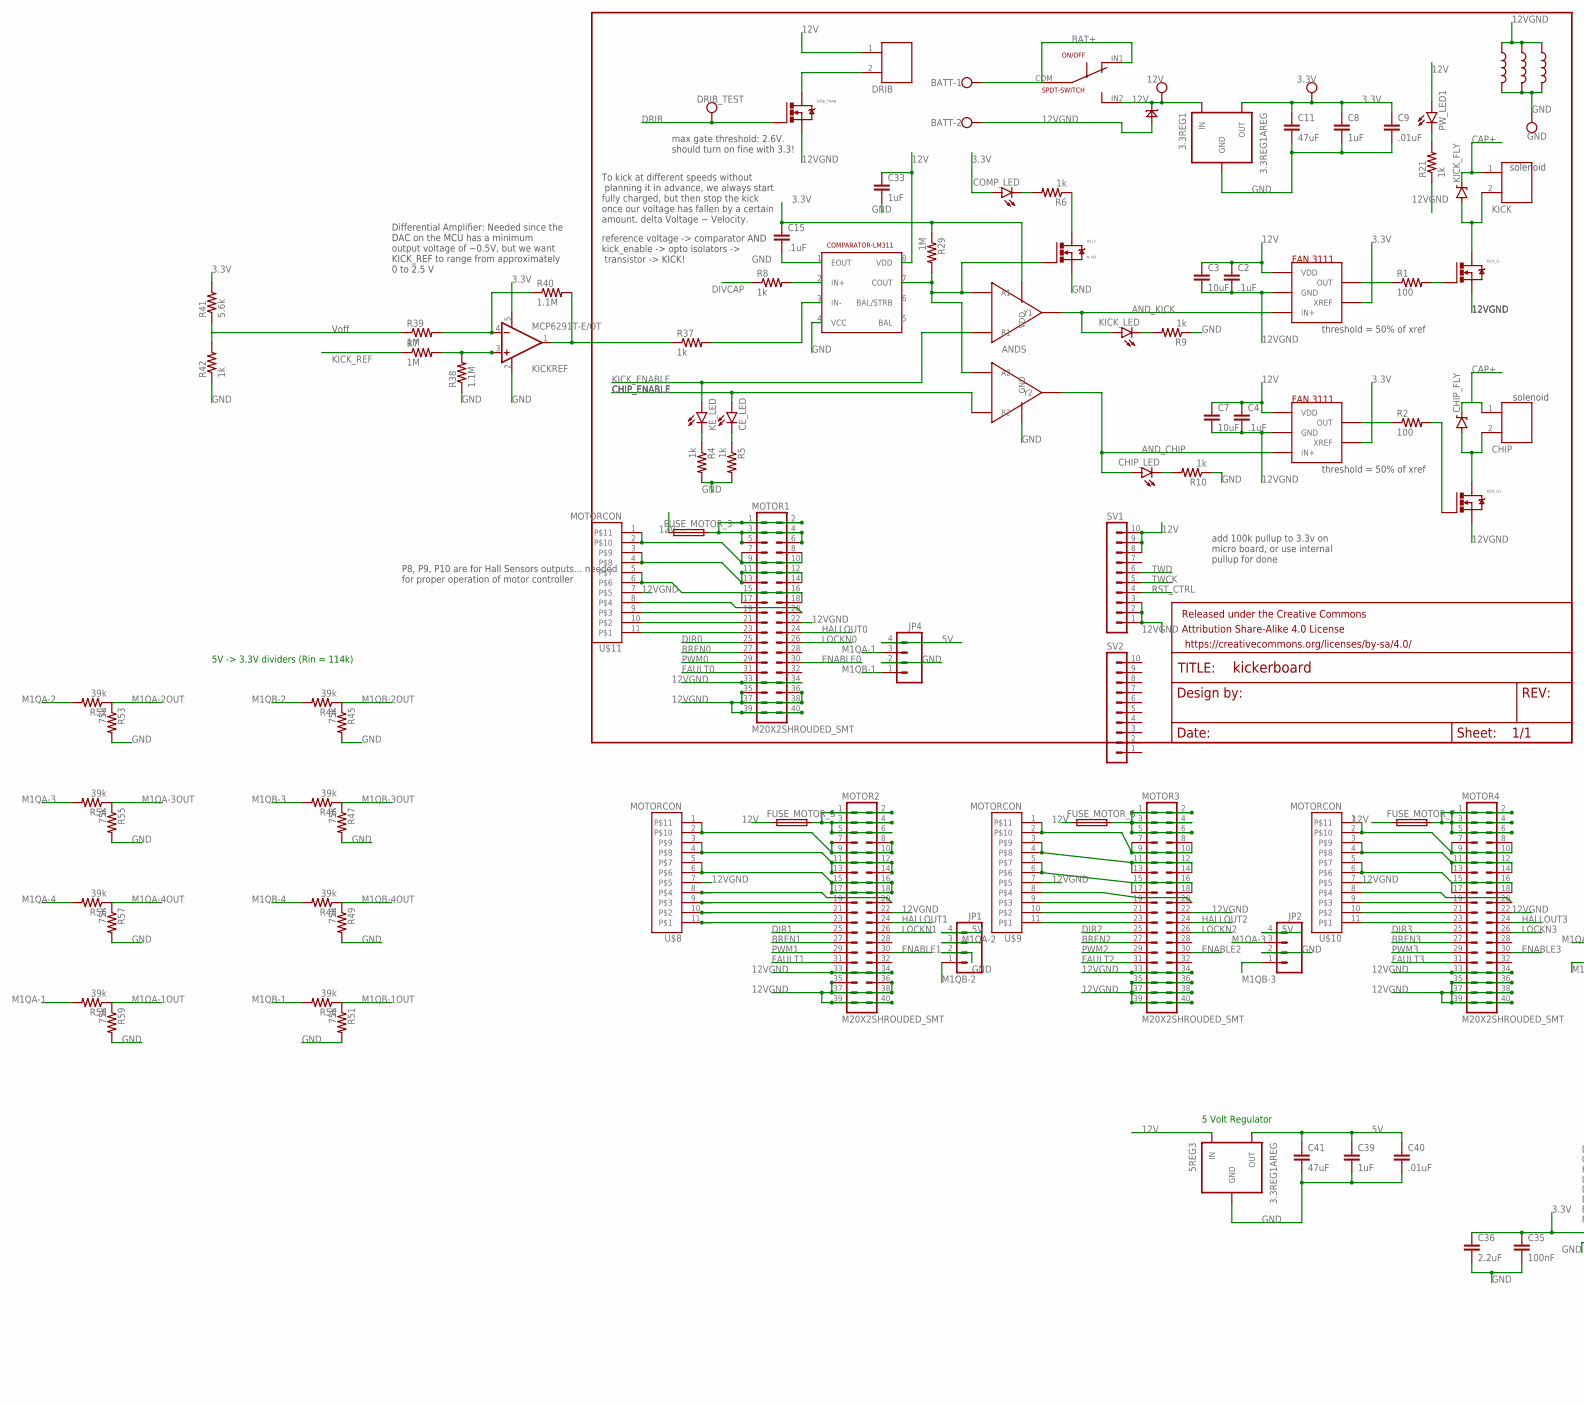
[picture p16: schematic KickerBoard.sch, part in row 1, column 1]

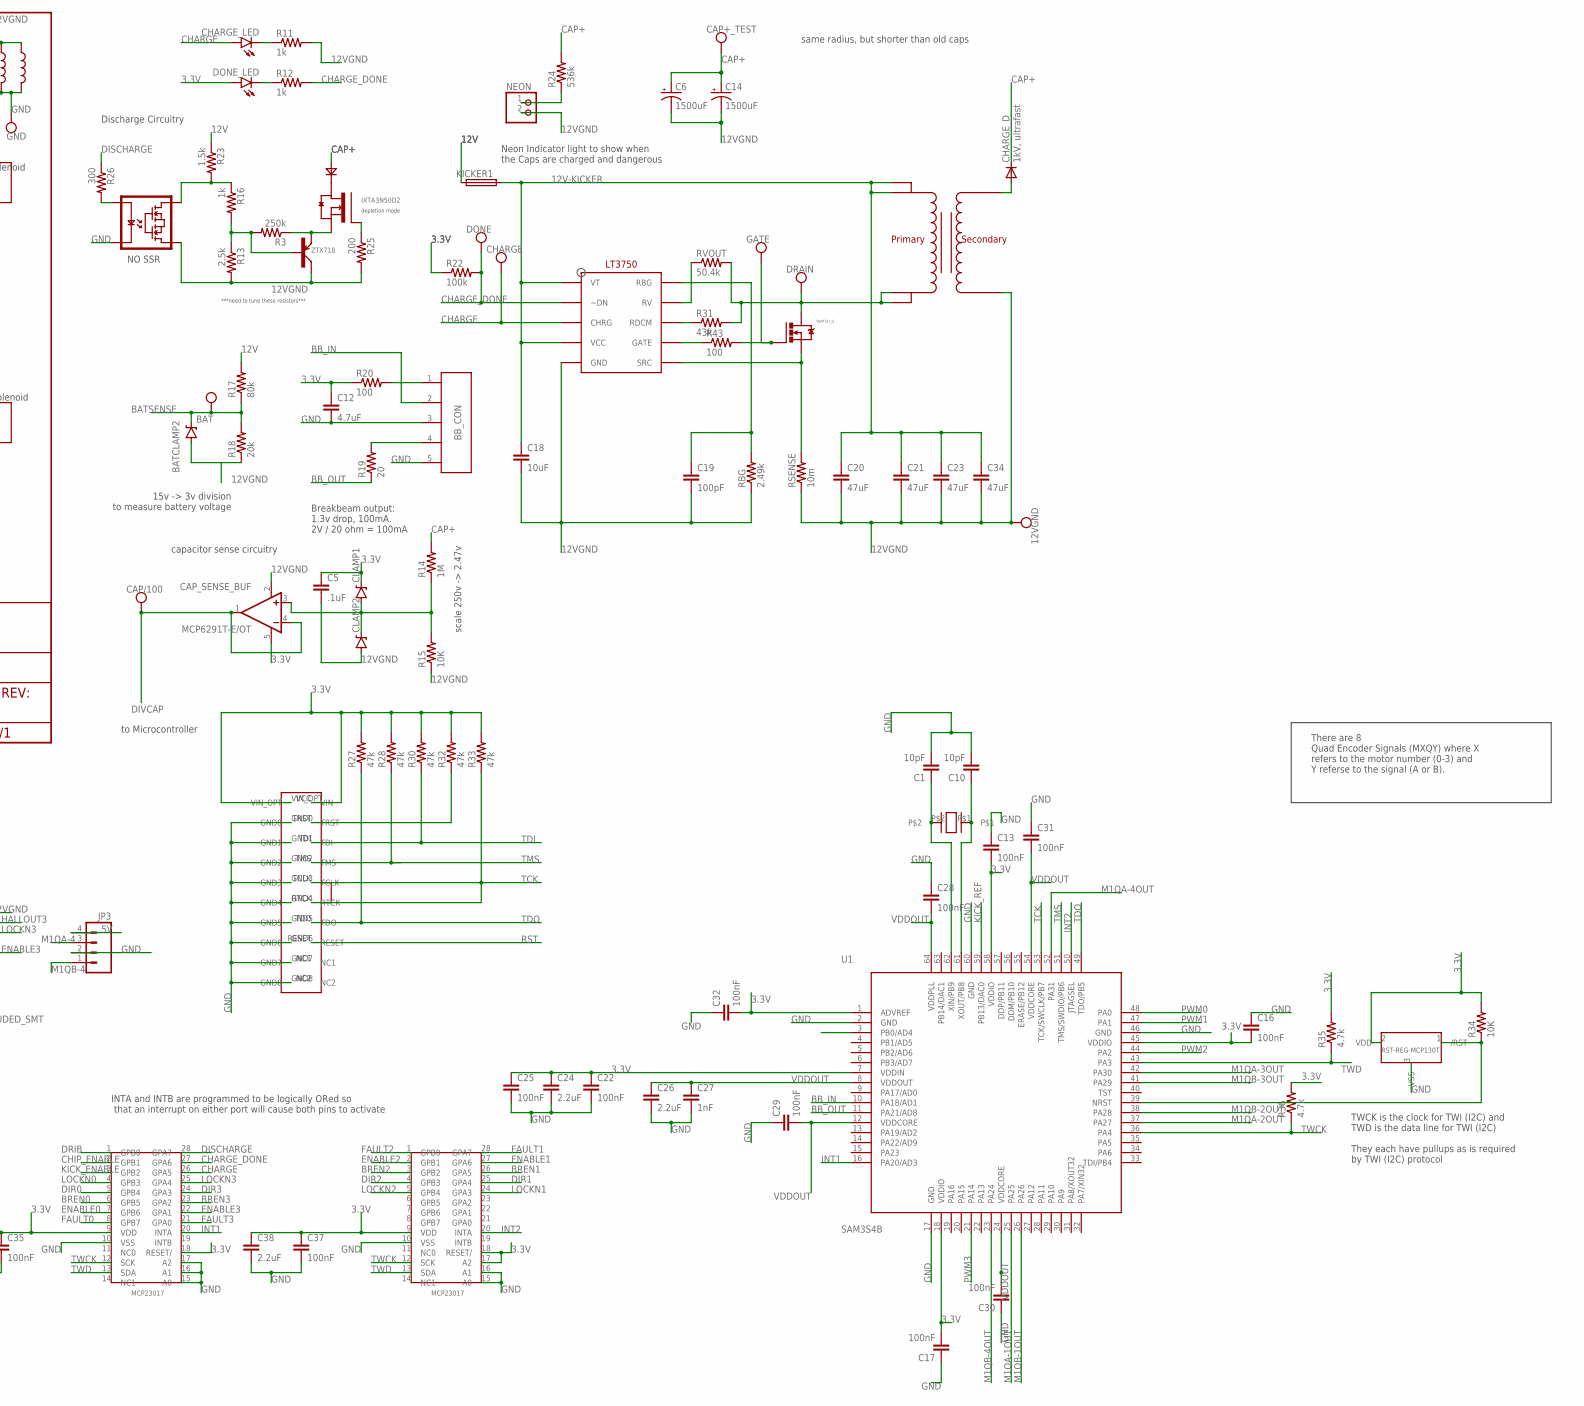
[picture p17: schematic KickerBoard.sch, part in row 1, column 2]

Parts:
3.3REG1, 5REG3: 3.3REG1AREG; DPAK
3.3V, 12V, 12VGND: TEST_PT; TESTING_PT
ANDS: AND-DUAL; TSSOP8
BAT: TEST_PT; TESTING_PT
BATCLAMP2: DIODE-ZENERDO214AC; DO214AC
BATT: W237-102
BB_CON: JST-5; JST-5-2MM
C1, C10: 10pF; 0805
C2, C4: .1uF; 1206
C3, C7: 10uF; 1206
C5, C15: .1uF; 0805
C6, C14: 1500uF; EB35D
C8, C39: 1uF; 0805
C9, C40: .01uF; 0805
C11, C20, C21, C23, C34, C41: 47uF; 1206
C12: 4.7uF; 0805
C13, C16, C17, C22, C25, C28, C29, C30, C31, C32, C35, C37: 100nF; 0805
C18: 10uF; 0805
C19: 100pF; 0805
C24, C26, C36, C38: 2.2uF; 0805
C27: 1nF; 0805
C33: 1uF; 1206
CAP+_TEST: TEST_PT; TESTING_PT
CAP/100: TEST_PT; TESTING_PT
CAP_SENSE_BUF: MCP6291T-E/OT; SOT23-5
CE_LED: LED1206; LED-1206
CHARGE: TEST_PT; TESTING_PT
CHARGE_D: 1kV, ultrafast; DO214AC
CHARGE_LED: LED1206; LED-1206
CHARGE_U: LT3750; 10-MSOP
CHIP: JST-22MM; JST-2-2MM
CHIP_FLY: DIODE-ZENERDO214AB; DO214AB
CHIP_LED: LED1206; LED-1206
CLAMP1, CLAMP2: DIODE-ZENERDO214AC; DO214AC
COMP_LED: LED1206; LED-1206
DONE: TEST_PT; TESTING_PT
DONE_LED: LED1206; LED-1206
DRAIN: TEST_PT; TESTING_PT
DRIB: JST-22MM; JST-2-2MM
DRIB_TEST: TEST_PT; TESTING_PT
DRIB_TRAN: N-MOSFETDPAK; DPAK
FRAME4: FRAME-LETTER; CREATIVE_COMMONS
FUSE_MOTOR_3, FUSE_MOTOR_5, FUSE_MOTOR_6, FUSE_MOTOR_7: TR5
GATE: TEST_PT; TESTING_PT
GND: TEST_PT; TESTING_PT
JP1, JP2, JP3, JP4: M04SMD_RA_FEMALE; 1X04_SMD_RA_FEMALE
KE_LED: LED1206; LED-1206
KICK: JST-22MM; JST-2-2MM
KICKER1: TR5
KICKREF: MCP6291T-E/OT; SOT23-5
KICK_FLY: DIODE-ZENERDO214AB; DO214AB
KICK_LED: LED1206; LED-1206
KICK_Q, KICK_Q1: N-MOSFETDPAK; DPAK
MOTOR1, MOTOR2, MOTOR3, MOTOR4: M20X2SHROUDED_SMT; 2X20_SHROUDED_SMT
NEON: PINHD-1X2; 1X02
ON/OFF: SPDT-SWITCH; CK_SWITCH
PW_LED1: LED1206; LED-1206
R1, R2, R20, R43: 100; 0805
R3: 250k; 0805
R4, R5, R6, R8, R9, R10, R11, R12, R16, R21, R37, R42: 1k; 0805
R7, R14, R29, R39: 1M; 0805
R13: 2.5k; 0805
R15, R34: 10K; 0805
R17: 80k; 0805
R18: 20k; 0805
R19: 20; 0805
R22: 100k; 0805
R23: 1.5k; 0805
R24: 536k; 0805
R25: 200; 0805
R26: 300; 0805
R27, R28, R30, R32, R33: 47k; 0805
R31: 43k; 0805
R35, R36: 4.7k; 0805
R38, R40: 1.1M; 0805
R41: 5.6k; 0805
R44, R46, R48, R50, R52, R54, R56, R58: 39k; 0805
R45, R47, R49, R51, R53, R55, R57, R59: 75k; 0805
RBG: 2.49k; 0805
RSENSE: 10m; R2512
RVOUT: 50.4k; 0805
SV1, SV2: MA10-1W
SWITCH_Q: N-MOSFETDPAK; DPAK
U1: SAM3S4B; LQFP64
U$1, U$4: FAN31111; SOT23-5
U$2: IXTA3N50D2; TO-263
U$3: 32052-TRANSFORMER; 10-TRANSFORMER
U$5: VO1400AEFTR; SOP4
U$6: ZTX718; TO92
U$7: 1N4007; THROUGH-HOLE-2
U$8, U$9, U$10, U$11: MOTORCON; GEN3CON
U$12: 13VZENER; THROUGH-HOLE-2
U$13, U$19, U$20: INDUCTOR; 0805
U$14: JTA-CONN; JTAG-CONN
U$15: 12MHZ-OSC; CRYSTAL-THRU-12MHZ
U$16: RST-REG; SOT23-3
U$17, U$21: IO-EXPANDER; SSOP
U$18: LM311; SOIC8
U$22: N-FET; SOT-23

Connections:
3.3V: 3.3REG1.SOURCE (OUT), 3.3V.P$1, ANDS.P$8 (VDD), C5.1, C8.1, C9.1, C11.1, C12.1, C13.2, C15.1, C16.2, C17.2, C22.1, C24.1, C25.1, C32.2, C35.1, C36.1, C37.1, C38.1, CAP_SENSE_BUF.5 (V+), CLAMP1.C, COMP_LED.A, DONE_LED.A, KICKREF.5 (V+), R20.1, R22.1, R27.2, R28.2, R29.1, R30.2, R32.2, R33.2, R34.2, R35.2, R36.2, R41.2, U1.1 (ADVREF), U1.7 (VDDIN), U1.18 (VDDIO), U1.45 (VDDIO), U1.58 (VDDIO), U$1.4 (XREF), U$4.4 (XREF), U$14.VCC (VIN), U$14.VIN_OPT, U$16.2 (VDD), U$17.9 (VDD), U$17.18 (RESET/), U$21.9 (VDD), U$21.17 (A2), U$21.18 (RESET/)
5V: 5REG3.SOURCE (OUT), C39.1, C40.1, C41.1, JP1.4, JP2.4, JP3.4, JP4.4
12V: 3.3REG1.GATE (IN), 5REG3.GATE (IN), 12V.P$1, C2.1, C3.1, C4.1, C7.1, C33.1, DRIB.1, FUSE_MOTOR_3.1, FUSE_MOTOR_5.1, FUSE_MOTOR_6.1, FUSE_MOTOR_7.1, KICKER1.1, ON/OFF.IN2 (P2), PW_LED1.A, R17.2, R23.1, SV1.8, SV1.9, SV1.10, U$1.1 (VDD), U$4.1 (VDD), U$12.-, U$18.8 (VDD)
12V-KICKER: C18.1, C20.1, C21.1, C23.1, C34.1, CHARGE_U.P$1 (VT), CHARGE_U.P$4 (VCC), KICKER1.2, U$3.P$4, U$3.P$5
12VGND: 12VGND.P$1, BATCLAMP2.A, BATT.2, C2.2, C3.2, C4.2, C5.2, C6.-, C7.2, C14.-, C18.2, C19.2, C20.2, C21.2, C23.2, C34.2, CAP_SENSE_BUF.2 (V-), CHARGE_U.P$5 (GND), CLAMP2.A, DRIB_TRAN.SOURCE (S), KICK_Q.SOURCE (S), KICK_Q1.SOURCE (S), MOTOR1.22, MOTOR1.33, MOTOR1.34, MOTOR1.35, MOTOR1.36, MOTOR1.37, MOTOR1.38, MOTOR1.39, MOTOR1.40, MOTOR2.22, MOTOR2.33, MOTOR2.34, MOTOR2.35, MOTOR2.36, MOTOR2.37, MOTOR2.38, MOTOR2.39, MOTOR2.40, MOTOR3.22, MOTOR3.33, MOTOR3.34, MOTOR3.35, MOTOR3.36, MOTOR3.37, MOTOR3.38, MOTOR3.39, MOTOR3.40, MOTOR4.22, MOTOR4.33, MOTOR4.34, MOTOR4.35, MOTOR4.36, MOTOR4.37, MOTOR4.38, MOTOR4.39, MOTOR4.40, NEON.2, R11.2, R13.2, R15.1, R18.1, R21.1, R25.2, RBG.1, RSENSE.1, SV1.1, SV1.2, SV1.3, U$1.2 (GND), U$3.P$10, U$4.2 (GND), U$5.3 (S2), U$6.LEFT (COLLECTOR), U$8.7, U$9.7, U$10.7, U$11.7, U$12.+, U$13.1, U$19.1, U$20.1
AND_CHIP: ANDS.P$3 (Y2), CHIP_LED.A, U$1.3 (IN+)
AND_KICK: ANDS.P$7 (Y1), KICK_LED.A, U$4.3 (IN+)
BAT+: BATT.1, ON/OFF.COM, ON/OFF.IN1 (P1)
BATSENSE: BAT.P$1, BATCLAMP2.C, R17.1, R18.2, U1.3 (PB0/AD4)
BB_IN: BB_CON.2, U1.10 (PA18/AD1)
BB_OUT: R19.1, U1.11 (PA21/AD8)
BREN0: MOTOR1.27, U$17.6 (GPB5)
BREN1: MOTOR2.27, U$21.26 (GPA5)
BREN2: MOTOR3.27, U$21.3 (GPB2)
BREN3: MOTOR4.27, U$17.23 (GPA2)
CAP+: C6.+, C14.+, CAP+_TEST.P$1, CHARGE_D.C, CHIP.1, CHIP_FLY.CATHODE (C), KICK.1, KICK_FLY.CATHODE (C), R14.2, R24.2, U$7.+ (D+)
CHARGE: CHARGE.P$1, CHARGE_LED.A, CHARGE_U.P$3 (CHRG), U$17.26 (GPA5)
CHARGE_DONE: CHARGE_U.P$2 (~DN), DONE.P$1, R12.2, R22.2, U$17.27 (GPA6)
CHIP_ENABLE: ANDS.P$6 (B2), CE_LED.A, U$17.2 (GPB1)
COMP_OUT: ANDS.P$1 (A1), ANDS.P$5 (A2), R29.2, U$18.7 (COUT), U$22.G
DIR0: MOTOR1.25, U$17.5 (GPB4)
DIR1: MOTOR2.25, U$21.25 (GPA4)
DIR2: MOTOR3.25, U$21.4 (GPB3)
DIR3: MOTOR4.25, U$17.24 (GPA3)
DISCHARGE: R26.1, U$17.28 (GPA7)
DIVCAP: CAP/100.P$1, CAP_SENSE_BUF.1 (OUT), CAP_SENSE_BUF.4 (-IN), R8.1
DRIB: DRIB_TEST.P$1, DRIB_TRAN.GATE (G), U$17.1 (GPB0)
ENABLE0: MOTOR1.30, U$17.7 (GPB6)
ENABLE1: MOTOR2.30, U$21.27 (GPA6)
ENABLE2: MOTOR3.30, U$21.2 (GPB1)
ENABLE3: MOTOR4.30, U$17.22 (GPA1)
FAULT0: MOTOR1.31, U$17.8 (GPB7)
FAULT1: MOTOR2.31, U$21.28 (GPA7)
FAULT2: MOTOR3.31, U$21.1 (GPB0)
FAULT3: MOTOR4.31, U$17.21 (GPA0)
GND: 3.3REG1.DRAIN (GND), 5REG3.DRAIN (GND), ANDS.P$4 (GND), BB_CON.3, BB_CON.5, C1.2, C8.2, C9.2, C10.2, C11.2, C12.2, C13.1, C15.2, C16.1, C17.1, C22.2, C24.2, C25.2, C26.2, C27.2, C28.1, C29.1, C30.1, C31.1, C32.1, C33.2, C35.2, C36.2, C37.2, C38.2, C39.2, C40.2, C41.2, GND.P$1, JP1.2, JP2.2, JP3.2, JP4.2, KICKREF.2 (V-), R4.2, R5.2, R9.1, R10.1, R38.1, R42.1, R45.2, R47.2, R49.2, R51.2, R53.2, R55.2, R57.2, R59.2, U1.2 (GND), U1.17 (GND), U1.46 (GND), U1.60 (GND), U$5.2 (LED-), U$13.2, U$14.GND0, U$14.GND1, U$14.GND2, U$14.GND3, U$14.GND4, U$14.GND5, U$14.GND6, U$14.GND7, U$14.GND8, U$16.3 (VSS), U$17.10 (VSS), U$17.15 (A0), U$17.16 (A1), U$17.17 (A2), U$18.1 (EOUT), U$18.4 (VCC), U$19.2, U$20.2, U$21.10 (VSS), U$21.15 (A0), U$21.16 (A1), U$22.S
HALLOUT0: MOTOR1.24
HALLOUT1: MOTOR2.24
HALLOUT2: MOTOR3.24
HALLOUT3: MOTOR4.24
INT1: U1.16 (PA20/AD3), U$17.20 (INTA)
INT2: U1.50 (JTAGSEL), U$21.20 (INTA)
KICK_ENABLE: ANDS.P$2 (B1), KE_LED.A, U$17.3 (GPB2)
KICK_REF: R7.1, U1.59 (PB13/DAC0)
LOCKN0: MOTOR1.26, U$17.4 (GPB3)
LOCKN1: MOTOR2.26, U$21.24 (GPA3)
LOCKN2: MOTOR3.26, U$21.5 (GPB4)
LOCKN3: MOTOR4.26, U$17.25 (GPA4)
LOWCHIP: CHIP.2, CHIP_FLY.ANODE (A), KICK_Q1.DRAIN (D)
LOWKICK: KICK.2, KICK_FLY.ANODE (A), KICK_Q.DRAIN (D)
M1QA-1: JP4.3, R58.2
M1QA-1OUT: R58.1, R59.1, U1.25 (PA25)
M1QA-2: JP1.3, R52.2
M1QA-2OUT: R52.1, R53.1, U1.37 (PA27)
M1QA-3: JP2.3, R54.2
M1QA-3OUT: R54.1, R55.1, U1.42 (PA30)
M1QA-4: JP3.3, R56.2
M1QA-4OUT: R56.1, R57.1, U1.52 (PA31)
M1QB-1: JP4.1, R50.2
M1QB-1OUT: R50.1, R51.1, U1.26 (PA26)
M1QB-2: JP1.1, R44.2
M1QB-2OUT: R44.1, R45.1, U1.38 (PA28)
M1QB-3: JP2.1, R46.2
M1QB-3OUT: R46.1, R47.1, U1.41 (PA29)
M1QB-4: JP3.1, R48.2
M1QB-4OUT: R48.1, R49.1, U1.23 (PA24)
unnamed: DRAIN.P$1, R31.2, RVOUT.2, SWITCH_Q.DRAIN (D), U$3.P$6, U$3.P$7
unnamed: R1.1, U$4.5 (OUT)
unnamed: KICK_Q1.GATE (G), R2.2
unnamed: FUSE_MOTOR_6.2, MOTOR3.1, MOTOR3.2, MOTOR3.3, MOTOR3.4, MOTOR3.5, MOTOR3.6
unnamed: R2.1, U$1.5 (OUT)
unnamed: CHARGE_U.P$8 (RDCM), R31.1
unnamed: C19.1, CHARGE_U.P$10 (RBG), RBG.2
unnamed: KICK_Q.GATE (G), R1.2
unnamed: GATE.P$1, R43.2, SWITCH_Q.GATE (G)
unnamed: R3.1, U$2.LOWER_RIGHT (SOURCE), U$6.RIGHT (EMITTER)
unnamed: KE_LED.C, R4.1
unnamed: CHARGE_U.P$9 (RV), RVOUT.1
unnamed: CE_LED.C, R5.1
unnamed: R6.1, U$22.D
unnamed: KICK_LED.C, R9.2
unnamed: C1.1, U1.62 (XIN/PB9), U$15.P$2
unnamed: CHIP_LED.C, R10.2
unnamed: R3.2, R13.1, R16.2, U$6.CENTER (BASE)
unnamed: DONE_LED.C, R12.1
unnamed: CHARGE_LED.C, R11.1
unnamed: R25.1, U$2.LOWER_LEFT (GATE)
unnamed: R32.1, U$14.TRST
unnamed: PW_LED1.C, R21.2
unnamed: CHARGE_U.P$6 (SRC), RSENSE.2, SWITCH_Q.SOURCE (S)
unnamed: FUSE_MOTOR_7.2, MOTOR4.1, MOTOR4.2, MOTOR4.3, MOTOR4.4, MOTOR4.5, MOTOR4.6
unnamed: FUSE_MOTOR_5.2, MOTOR2.1, MOTOR2.2, MOTOR2.3, MOTOR2.4, MOTOR2.5, MOTOR2.6
unnamed: FUSE_MOTOR_3.2, MOTOR1.1, MOTOR1.2, MOTOR1.3, MOTOR1.4, MOTOR1.5, MOTOR1.6
unnamed: MOTOR3.15, MOTOR3.16, MOTOR3.17, MOTOR3.18, U$9.5, U$9.6
unnamed: R16.1, R23.2, U$5.4 (S1)
unnamed: R26.2, U$5.1 (LED+)
unnamed: C10.1, U1.61 (XOUT/PB8), U$15.P$1
unnamed: BB_CON.4, R19.2
unnamed: COMP_LED.C, R6.2
unnamed: CHARGE_U.P$7 (GATE), R43.1
unnamed: R8.2, U$18.2 (IN+)
unnamed: U$2.TAB (DRAIN), U$7.- (D-)
unnamed: MOTOR3.11, MOTOR3.12, MOTOR3.13, MOTOR3.14, U$9.3, U$9.4
unnamed: MOTOR3.7, MOTOR3.8, MOTOR3.9, MOTOR3.10, U$9.1, U$9.2
unnamed: MOTOR1.15, MOTOR1.16, MOTOR1.17, MOTOR1.18, U$11.5, U$11.6
unnamed: BB_CON.1, R20.2
unnamed: KICKREF.3 (+IN), R7.2, R38.2
unnamed: MOTOR2.20, U$8.8
unnamed: MOTOR2.19, U$8.9
unnamed: MOTOR2.21, U$8.10
unnamed: MOTOR2.23, U$8.11
unnamed: MOTOR2.7, MOTOR2.8, MOTOR2.9, MOTOR2.10, U$8.1, U$8.2
unnamed: MOTOR2.11, MOTOR2.12, MOTOR2.13, MOTOR2.14, U$8.3, U$8.4
unnamed: MOTOR2.15, MOTOR2.16, MOTOR2.17, MOTOR2.18, U$8.5, U$8.6
unnamed: KICKREF.1 (OUT), R37.1, R40.2
unnamed: MOTOR1.20, U$11.8
unnamed: MOTOR1.19, U$11.9
unnamed: MOTOR1.21, U$11.10
unnamed: MOTOR1.23, U$11.11
unnamed: MOTOR4.15, MOTOR4.16, MOTOR4.17, MOTOR4.18, U$10.5, U$10.6
unnamed: MOTOR4.11, MOTOR4.12, MOTOR4.13, MOTOR4.14, U$10.3, U$10.4
unnamed: MOTOR4.7, MOTOR4.8, MOTOR4.9, MOTOR4.10, U$10.1, U$10.2
unnamed: R39.1, R41.1, R42.2
unnamed: MOTOR3.20, U$9.8
unnamed: MOTOR3.19, U$9.9
unnamed: MOTOR3.21, U$9.10
unnamed: MOTOR3.23, U$9.11
unnamed: R37.2, U$18.3 (IN-)
unnamed: MOTOR4.20, U$10.8
unnamed: MOTOR4.19, U$10.9
unnamed: MOTOR4.21, U$10.10
unnamed: MOTOR4.23, U$10.11
unnamed: KICKREF.4 (-IN), R39.2, R40.1
unnamed: MOTOR1.11, MOTOR1.12, MOTOR1.13, MOTOR1.14, U$11.3, U$11.4
unnamed: MOTOR1.7, MOTOR1.8, MOTOR1.9, MOTOR1.10, U$11.1, U$11.2
PWM0: MOTOR1.29, U1.48 (PA0)
PWM1: MOTOR2.29, U1.47 (PA1)
PWM2: MOTOR3.29, U1.44 (PA2)
PWM3: MOTOR4.29, U1.21 (PA14)
RST: R34.1, U1.39 (NRST), U$14.RESET, U$16.1 (/RST)
RST_CTRL: SV1.4
TCK: R33.1, U1.53 (TCK/SWCLK/PB7), U$14.RTCK, U$14.TCLK
TDI: R30.1, U$14.TDI
TDO: R27.1, U1.49 (TDO/PB5), U$14.TDO
TMS: R28.1, U1.51 (TMS/SWDIO/PB6), U$14.TMS
TO_DRIB: DRIB.2, DRIB_TRAN.DRAIN (D)
TO_NEON: NEON.1, R24.1
TRANS_OUT: CHARGE_D.A, U$3.P$1
TWCK: R36.1, SV1.5, U1.36 (PA4), U$17.12 (SCK), U$21.12 (SCK)
TWD: R35.1, SV1.6, U1.43 (PA3), U$17.13 (SDA), U$21.13 (SDA)
UNBUF_DIVCAP: CAP_SENSE_BUF.3 (+IN), CLAMP1.A, CLAMP2.C, R14.1, R15.2
VDDOUT: C26.1, C27.1, C28.2, C29.2, C30.2, C31.2, U1.8 (VDDOUT), U1.12 (VDDCORE), U1.24 (VDDCORE), U1.54 (VDDCORE), U1.64 (VDDPLL)

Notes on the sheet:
scale 250v -> 2.47v
To kick at different speeds without planning it in advance, we always start fully charged, but then stop the kick once our voltage has fallen by a certain amount. delta Voltage ~ Velocity.
reference voltage -> comparator AND kick_enable -> opto isolators -> transistor -> KICK!
add 100k pullup to 3.3v on micro board, or use internal pullup for done
Neon Indicator light to show when the Caps are charged and dangerous
to Microcontroller
threshold = 50% of xref
same radius, but shorter than old caps
Discharge Circuitry
capacitor sense circuitry
15v -> 3v division to measure battery voltage
max gate threshold: 2.6V. should turn on fine with 3.3!
Breakbeam output: 1.3v drop, 100mA. 2V / 20 ohm = 100mA
solenoid
IXTA3N50D2
ZTX718
***need to tune these resistors***
depletion mode
NO SSR
TWCK is the clock for TWI (I2C) and TWD is the data line for TWI (I2C) They each have pullups as is required by TWI (I2C) protocol
There are 8 Quad Encoder Signals (MXQY) where X refers to the motor number (0-3) and Y referse to the signal (A or B).
Voff
Differential Amplifier: Needed since the DAC on the MCU has a minimum output voltage of ~0.5V, but we want KICK_REF to range from approximately 0 to 2.5 V
P8, P9, P10 are for Hall Sensors outputs... needed for proper operation of motor controller
INTA and INTB are programmed to be logically ORed so that an interrupt on either port will cause both pins to activate
5 Volt Regulator
5V -> 3.3V dividers (Rin = 114k)

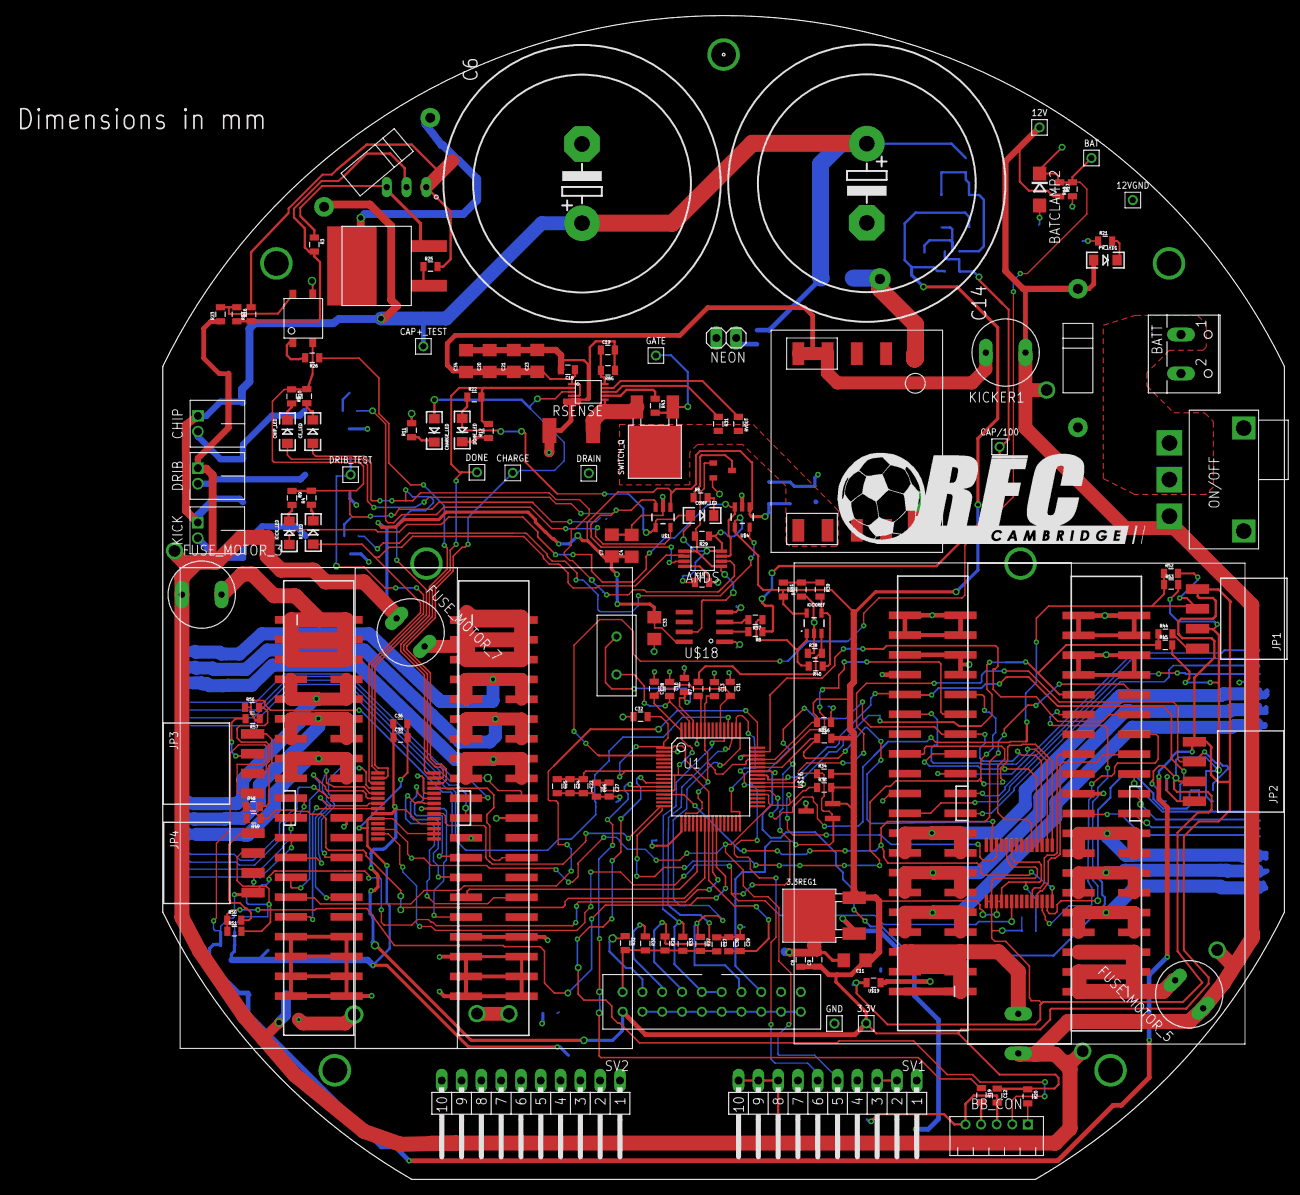
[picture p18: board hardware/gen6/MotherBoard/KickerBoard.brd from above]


Board: 4 copper layers, 143.9 x 149.3 mm, 185 parts (36 on the bottom side), 147 nets.

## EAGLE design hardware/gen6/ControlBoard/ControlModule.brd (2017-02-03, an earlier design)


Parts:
3.3REG: 3.3REG1AREG; DPAK
C4, C10: 47uF; 1206
C5, C12, C13: 1uF; 0805
C6, C7, C11: 0.01uF; 0805
C8: 10uF; 0805
C9, C14: 0.1uF; 0805
FRAME1: FRAME-LETTER; CREATIVE_COMMONS
PWR_LED: LED1206; LED-1206
Q1, Q2: BSS123; SOT23
R1, R6, R7, R10: 100; 0805
R2, R5, R8, R9: 10k; 0805
R3, R4: 0; 0805
R13, R14, R15, R16: 1k; 0805
RX: TEST_PT; TESTING_PT
RX_LED: LED1206; LED-1206
S2, S4: TAC_SWITCHSMD; TACTILE-SWITCH-SMD
SCK_LED: LED1206; LED-1206
SV1: ICSP; MA03-2
SV2, SV3: MA10-1W
TX: TEST_PT; TESTING_PT
TX_LED: LED1206; LED-1206
U1: ATMEGA328P-AU; QFP80P900X900X120-32N
U$1: 4-POS-DIP; 4-POS-DIP-SMD
U$2: INDUCTOR; 0805
XBEE: XBEE-1B1; XBEE-1

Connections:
3.3V: 3.3REG.SOURCE (OUT), C7.1, C8.1, C9.1, C10.1, C11.2, C12.2, C13.1, C14.1, R2.2, R5.2, R16.2, S2.3, S2.4, S4.1, S4.2, SV1.2, U1.4 (VCC_2), U1.6 (VCC), U1.18 (AVCC), U1.20 (AREF), XBEE.1 (VDD)
12V: 3.3REG.GATE (IN), C4.1, C5.1, C6.1, SV2.8, SV2.9, SV2.10
12VGND: C4.2, C5.2, C6.2, SV2.1, SV2.2, SV2.3, U$2.1
BID0: U1.8 (PB7), U$1.1 (1A)
BID1: U1.9 (PD5), U$1.2 (2A)
BID2: U1.10 (PD6), U$1.3 (3A)
BID3: U1.11 (PD7), U$1.4 (4A)
CTS: R4.1, U1.1 (PD3)
GND: 3.3REG.DRAIN (GND), C7.2, C8.2, C9.2, C10.2, C11.1, C12.1, C13.2, C14.2, PWR_LED.C, Q1.2 (S), Q2.2 (S), R8.1, R9.2, RX_LED.C, SCK_LED.C, SV1.6, TX_LED.C, U1.3 (GND_2), U1.5 (GND_3), U1.21 (GND), U$1.5 (4B), U$1.6 (3B), U$1.7 (2B), U$1.8 (1B), U$2.2, XBEE.10 (GND)
MISO: SV1.1, U1.16 (PB4)
MOSI: SV1.4, U1.15 (PB3)
unnamed: R3.2, XBEE.16 (RTS)
unnamed: R13.1, SCK_LED.A
unnamed: R4.2, XBEE.12 (CTS)
unnamed: R1.1, U1.27 (PC4)
unnamed: R10.1, U1.23 (PC0)
unnamed: R6.1, U1.28 (PC5)
unnamed: R14.1, TX_LED.A
unnamed: R15.1, RX_LED.A
unnamed: PWR_LED.A, R16.1
unnamed: Q2.1 (G), R8.2, R10.2, S4.3, S4.4
unnamed: Q1.1 (G), R7.1, R9.1, S2.1, S2.2
RST: Q1.3 (D), R2.1, SV1.5, U1.29 (PC6)
RST_CTRL: R7.2, SV2.4
RTS: R3.1, U1.32 (PD2)
RX: R15.2, RX.P$1, U1.30 (PD0), XBEE.2 (DOUT)
SCK: R13.2, SV1.3, U1.17 (PB5)
TWCK: R6.2, SV2.5
TWD: R1.2, SV2.6
TX: R14.2, TX.P$1, U1.31 (PD1), XBEE.3 (DIN)
XBRST: Q2.3 (D), R5.1, XBEE.5 (RESET)

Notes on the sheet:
RTS/CTS likely not necessary, but can be connected if needed.



Board: 2 copper layers, 42.8 x 65.3 mm, 44 parts (21 on the bottom side), 31 nets.

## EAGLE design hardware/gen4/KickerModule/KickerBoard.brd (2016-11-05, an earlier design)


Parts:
3.3REG1: 3.3REG1AREG; DPAK
3.3V_TEST, 12VGND_TEST, 12V_TEST: TEST_PT; TESTING_PT
ANDS: AND-DUAL; TSSOP8
BATCLAMP2: DIODE-ZENERDO214AC; DO214AC
BATSENSE_TEST: TEST_PT; TESTING_PT
BATT: W237-102
BB_CON: JST-5; JST-5-2MM
C2, C4: .1uF; 1206
C3, C7: 10uF; 1206
C5, C15: .1uF; 0805
C6, C14: 1500uF; EB35D
C8: 1uF; 0805
C9: .01uF; 0805
C11, C20, C21, C23: 47uF; 1206
C12: 4.7uF; 0805
C18: 10uF; 0805
C19: 100pF; 0805
CAP+_TEST: TEST_PT; TESTING_PT
CAP/100: TEST_PT; TESTING_PT
CAP_COMP: LM331; SOT23-5
CAP_SENSE_BUF: MCP6291T-E/OT; SOT23-5
CE_LED: LED1206; LED-1206
CHARGE_D: 1kV, ultrafast; DO214AC
CHARGE_LED: LED1206; LED-1206
CHARGE_TEST: TEST_PT; TESTING_PT
CHARGE_U: LT3750; 10-MSOP
CHIP: JST-22MM; JST-2-2MM
CHIP_FLY: DIODE-ZENERDO214AB; DO214AB
CHIP_LED: LED1206; LED-1206
CLAMP1, CLAMP2: DIODE-ZENERDO214AC; DO214AC
COMP_LED: LED1206; LED-1206
COMS_BOARD_FUSE: TR5
COM_BOARD: M20X2SHROUDED_SMT; 2X20_SHROUDED_SMT
DONE_LED: LED1206; LED-1206
DONE_TEST: TEST_PT; TESTING_PT
DRAIN_TEST: TEST_PT; TESTING_PT
DRIB: JST-22MM; JST-2-2MM
DRIB_TEST: TEST_PT; TESTING_PT
DRIB_TRAN: N-MOSFETDPAK; DPAK
FRAME4: FRAME-LETTER; CREATIVE_COMMONS
FUSE_MOTOR_3, FUSE_MOTOR_5, FUSE_MOTOR_6, FUSE_MOTOR_7: TR5
GATE_TEST: TEST_PT; TESTING_PT
GND_TEST: TEST_PT; TESTING_PT
JP1, JP2, JP3, JP4: M04SMD_RA_FEMALE; 1X04_SMD_RA_FEMALE
KE_LED: LED1206; LED-1206
KICK: JST-22MM; JST-2-2MM
KICKER1: TR5
KICK_FLY: DIODE-ZENERDO214AB; DO214AB
KICK_LED: LED1206; LED-1206
KICK_Q, KICK_Q1: N-MOSFETDPAK; DPAK
MOTOR1, MOTOR2, MOTOR3, MOTOR4: M20X2SHROUDED_SMT; 2X20_SHROUDED_SMT
NEON: PINHD-1X2; 1X02
ON/OFF: SPDT-SWITCH; CK_SWITCH
PW_LED1: LED1206; LED-1206
R1, R2, R20: 100; 0805
R3: 250k; 0805
R4, R5, R6, R9, R10, R11, R12, R16, R21, R22: 1k; 0805
R7: 100k; 0805
R8: 3k; 0805
R13: 2.5k; 0805
R14: 1M; 0805
R15: 10K; 0805
R17: 80k; 0805
R18: 20k; 0805
R19: 20; 0805
R23: 1.5k; 0805
R24: 536k; 0805
R25: 200; 0805
R26: 300; 0805
R29: 10k; 0805
R31: 43k; 0805
RBG: 2.49k; 0805
RSENSE: 10m; R2512
RVOUT: 50.4k; 0805
SWITCH_Q: N-MOSFETDPAK; DPAK
U$1, U$4: FAN31111; SOT23-5
U$2: IXTA3N50D2; TO-263
U$3: 32052-TRANSFORMER; 10-TRANSFORMER
U$5: VO1400AEFTR; SOP4
U$6: ZTX718; TO92
U$7: 1N4007; THROUGH-HOLE-2
U$8, U$9, U$10, U$11: MOTORCON; GEN3CON
U$12: 13VZENER; THROUGH-HOLE-2
U$13: INDUCTOR; 0805

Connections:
3.3V: 3.3REG1.SOURCE (OUT), 3.3V_TEST.P$1, ANDS.P$8 (VDD), C5.1, C8.1, C9.1, C11.1, C12.1, C15.1, CAP_COMP.5 (V+), CAP_SENSE_BUF.5 (V+), CLAMP1.C, JP1.4, JP2.4, JP3.4, JP4.4, MOTOR1.26, MOTOR2.26, MOTOR3.26, MOTOR4.26, PW_LED1.A, R20.1, R22.1, R29.1, U$1.4 (XREF), U$4.4 (XREF)
12V: 3.3REG1.GATE (IN), 12V_TEST.P$1, C2.1, C3.1, C4.1, C7.1, COMS_BOARD_FUSE.1, DRIB.1, FUSE_MOTOR_3.1, FUSE_MOTOR_5.1, FUSE_MOTOR_6.1, FUSE_MOTOR_7.1, KICKER1.1, ON/OFF.IN2 (P2), R17.2, R23.1, U$1.1 (VDD), U$4.1 (VDD), U$12.-
12V-KICKER: C18.1, C20.1, C21.1, C23.1, CHARGE_U.P$1 (VT), CHARGE_U.P$4 (VCC), KICKER1.2, U$3.P$4, U$3.P$5
12VGND: 3.3REG1.DRAIN (GND), 12VGND_TEST.P$1, BATT.2, C2.2, C3.2, C4.2, C6.-, C7.2, C8.2, C9.2, C11.2, C14.-, C20.2, C21.2, C23.2, COM_BOARD.35, COM_BOARD.36, COM_BOARD.37, COM_BOARD.38, COM_BOARD.39, COM_BOARD.40, DRIB_TRAN.SOURCE (S), KICK_Q.SOURCE (S), KICK_Q1.SOURCE (S), MOTOR1.35, MOTOR1.36, MOTOR1.37, MOTOR1.38, MOTOR1.39, MOTOR1.40, MOTOR2.35, MOTOR2.36, MOTOR2.37, MOTOR2.38, MOTOR2.39, MOTOR2.40, MOTOR3.35, MOTOR3.36, MOTOR3.37, MOTOR3.38, MOTOR3.39, MOTOR3.40, MOTOR4.35, MOTOR4.36, MOTOR4.37, MOTOR4.38, MOTOR4.39, MOTOR4.40, NEON.2, R13.2, R15.1, R25.2, RSENSE.1, U$1.2 (GND), U$3.P$10, U$4.2 (GND), U$5.3 (S2), U$6.LEFT (COLLECTOR), U$12.+, U$13.1
AND_CHIP: ANDS.P$3 (Y2), CHIP_LED.A, U$1.3 (IN+)
AND_KICK: ANDS.P$7 (Y1), KICK_LED.A, U$4.3 (IN+)
BAT+: BATT.1, ON/OFF.COM, ON/OFF.IN1 (P1)
BATSENSE: BATCLAMP2.C, BATSENSE_TEST.P$1, R17.1, R18.2
BB_IN: BB_CON.2, COM_BOARD.7
BB_OUT: COM_BOARD.9, R19.1
CAP+: C6.+, C14.+, CAP+_TEST.P$1, CHARGE_D.C, CHIP.1, CHIP_FLY.CATHODE (C), KICK.1, KICK_FLY.CATHODE (C), R14.2, R24.2, U$7.+ (D+)
CHARGE: CHARGE_LED.A, CHARGE_TEST.P$1, CHARGE_U.P$3 (CHRG), COM_BOARD.19
CHARGE_DONE: CHARGE_U.P$2 (~DN), COM_BOARD.17, DONE_LED.A, DONE_TEST.P$1, R22.2
CHIP_ENABLE: ANDS.P$6 (B2), CE_LED.A, COM_BOARD.13
COMP_OUT: ANDS.P$1 (A1), ANDS.P$5 (A2), CAP_COMP.4 (OUT), COMP_LED.A, R7.1, R29.2
DISCHARGE: COM_BOARD.16, R26.1
DIVCAP: CAP/100.P$1, CAP_SENSE_BUF.1 (OUT), CAP_SENSE_BUF.4 (-IN), COM_BOARD.14, R8.2
DRIB: COM_BOARD.18, DRIB_TEST.P$1, DRIB_TRAN.GATE (G)
GND: ANDS.P$4 (GND), BATCLAMP2.A, BB_CON.3, BB_CON.5, C5.2, C12.2, C15.2, C18.2, C19.2, CAP_COMP.2 (V-), CAP_SENSE_BUF.2 (V-), CHARGE_U.P$5 (GND), CLAMP2.A, COM_BOARD.33, COM_BOARD.34, GND_TEST.P$1, JP1.2, JP2.2, JP3.2, JP4.2, MOTOR1.22, MOTOR1.30, MOTOR1.33, MOTOR1.34, MOTOR2.22, MOTOR2.30, MOTOR2.33, MOTOR2.34, MOTOR3.22, MOTOR3.30, MOTOR3.33, MOTOR3.34, MOTOR4.22, MOTOR4.30, MOTOR4.33, MOTOR4.34, R4.2, R5.2, R6.1, R9.1, R10.1, R11.2, R12.2, R18.1, R21.1, RBG.1, U$5.2 (LED-), U$8.5, U$9.5, U$10.5, U$11.5, U$13.2
HYSTERESIS: CAP_COMP.1 (IN+), R7.2, R8.1
KICK_ENABLE: ANDS.P$2 (B1), COM_BOARD.11, KE_LED.A
KICK_REF: CAP_COMP.3 (IN-), COM_BOARD.15
LOWCHIP: CHIP.2, CHIP_FLY.ANODE (A), KICK_Q1.DRAIN (D)
LOWKICK: KICK.2, KICK_FLY.ANODE (A), KICK_Q.DRAIN (D)
M1QA-1: JP4.3, MOTOR1.28
M1QA-2: JP1.3, MOTOR2.28
M1QA-3: JP2.3, MOTOR3.28
M1QA-4: JP3.3, MOTOR4.28
M1QB-1: JP4.1, MOTOR1.32
M1QB-2: JP1.1, MOTOR2.32
M1QB-3: JP2.1, MOTOR3.32
M1QB-4: JP3.1, MOTOR4.32
MISO: COM_BOARD.32, MOTOR1.27, MOTOR2.27, MOTOR3.27, MOTOR4.27
MOSI: COM_BOARD.30, MOTOR1.25, MOTOR2.25, MOTOR3.25, MOTOR4.25
unnamed: DRAIN_TEST.P$1, R31.2, RVOUT.2, SWITCH_Q.DRAIN (D), U$3.P$6, U$3.P$7
unnamed: R1.1, U$4.5 (OUT)
unnamed: KICK_Q1.GATE (G), R2.2
unnamed: FUSE_MOTOR_6.2, MOTOR3.1, MOTOR3.2, MOTOR3.3, MOTOR3.4, MOTOR3.5, MOTOR3.6
unnamed: R2.1, U$1.5 (OUT)
unnamed: CHARGE_U.P$8 (RDCM), R31.1
unnamed: C19.1, CHARGE_U.P$10 (RBG), RBG.2
unnamed: KICK_Q.GATE (G), R1.2
unnamed: CHARGE_U.P$7 (GATE), GATE_TEST.P$1, SWITCH_Q.GATE (G)
unnamed: R3.1, U$2.LOWER_RIGHT (SOURCE), U$6.RIGHT (EMITTER)
unnamed: KE_LED.C, R4.1
unnamed: CHARGE_U.P$9 (RV), RVOUT.1
unnamed: CE_LED.C, R5.1
unnamed: COMP_LED.C, R6.2
unnamed: KICK_LED.C, R9.2
unnamed: CHIP_LED.C, R10.2
unnamed: R3.2, R13.1, R16.2, U$6.CENTER (BASE)
unnamed: DONE_LED.C, R12.1
unnamed: CHARGE_LED.C, R11.1
unnamed: R25.1, U$2.LOWER_LEFT (GATE)
unnamed: PW_LED1.C, R21.2
unnamed: CHARGE_U.P$6 (SRC), RSENSE.2, SWITCH_Q.SOURCE (S)
unnamed: FUSE_MOTOR_7.2, MOTOR4.1, MOTOR4.2, MOTOR4.3, MOTOR4.4, MOTOR4.5, MOTOR4.6
unnamed: FUSE_MOTOR_5.2, MOTOR2.1, MOTOR2.2, MOTOR2.3, MOTOR2.4, MOTOR2.5, MOTOR2.6
unnamed: FUSE_MOTOR_3.2, MOTOR1.1, MOTOR1.2, MOTOR1.3, MOTOR1.4, MOTOR1.5, MOTOR1.6
unnamed: COMS_BOARD_FUSE.2, COM_BOARD.1, COM_BOARD.3, COM_BOARD.5
unnamed: R16.1, R23.2, U$5.4 (S1)
unnamed: R26.2, U$5.1 (LED+)
unnamed: BB_CON.4, R19.2
unnamed: U$2.TAB (DRAIN), U$7.- (D-)
unnamed: MOTOR2.7, MOTOR2.8, MOTOR2.9, MOTOR2.10, U$8.10, U$8.11
unnamed: MOTOR2.11, MOTOR2.12, MOTOR2.13, MOTOR2.14, U$8.8, U$8.9
unnamed: MOTOR2.15, MOTOR2.16, MOTOR2.17, MOTOR2.18, U$8.6, U$8.7
unnamed: BB_CON.1, R20.2
unnamed: MOTOR2.20, U$8.4
unnamed: MOTOR2.19, U$8.3
unnamed: MOTOR2.21, U$8.2
unnamed: MOTOR2.23, U$8.1
unnamed: MOTOR1.7, MOTOR1.8, MOTOR1.9, MOTOR1.10, U$11.10, U$11.11
unnamed: MOTOR1.11, MOTOR1.12, MOTOR1.13, MOTOR1.14, U$11.8, U$11.9
unnamed: MOTOR1.15, MOTOR1.16, MOTOR1.17, MOTOR1.18, U$11.6, U$11.7
unnamed: MOTOR1.20, U$11.4
unnamed: MOTOR1.19, U$11.3
unnamed: MOTOR1.21, U$11.2
unnamed: MOTOR1.23, U$11.1
unnamed: MOTOR3.7, MOTOR3.8, MOTOR3.9, MOTOR3.10, U$9.10, U$9.11
unnamed: MOTOR3.11, MOTOR3.12, MOTOR3.13, MOTOR3.14, U$9.8, U$9.9
unnamed: MOTOR3.15, MOTOR3.16, MOTOR3.17, MOTOR3.18, U$9.6, U$9.7
unnamed: MOTOR3.20, U$9.4
unnamed: MOTOR3.19, U$9.3
unnamed: MOTOR3.21, U$9.2
unnamed: MOTOR3.23, U$9.1
unnamed: MOTOR4.7, MOTOR4.8, MOTOR4.9, MOTOR4.10, U$10.10, U$10.11
unnamed: MOTOR4.11, MOTOR4.12, MOTOR4.13, MOTOR4.14, U$10.8, U$10.9
unnamed: MOTOR4.15, MOTOR4.16, MOTOR4.17, MOTOR4.18, U$10.6, U$10.7
unnamed: MOTOR4.20, U$10.4
unnamed: MOTOR4.19, U$10.3
unnamed: MOTOR4.21, U$10.2
unnamed: MOTOR4.23, U$10.1
SCK: COM_BOARD.28, MOTOR1.29, MOTOR2.29, MOTOR3.29, MOTOR4.29
SS1: COM_BOARD.20, MOTOR1.31
SS2: COM_BOARD.22, MOTOR2.31
SS3: COM_BOARD.24, MOTOR3.31
SS4: COM_BOARD.26, MOTOR4.31
TO_DRIB: DRIB.2, DRIB_TRAN.DRAIN (D)
TO_NEON: NEON.1, R24.1
TRANS_OUT: CHARGE_D.A, U$3.P$1
UNBUF_DIVCAP: CAP_SENSE_BUF.3 (+IN), CLAMP1.A, CLAMP2.C, R14.1, R15.2

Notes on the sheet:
scale 250v -> 2.47v
To kick at different speeds without planning it in advance, we always start fully charged, but then stop the kick once our voltage has fallen by a certain amount. delta Voltage ~ Velocity.
reference voltage -> comparator AND kick_enable -> opto isolators -> transistor -> KICK!
add 100k pullup to 3.3v on micro board, or use internal pullup for done
Neon Indicator light to show when the Caps are charged and dangerous
to Microcontroller
threshold = 50% of xref
same radius, but shorter than old caps
Discharge Circuitry
capacitor sense circuitry
15v -> 3v division to measure battery voltage
max gate threshold: 2.6V. should turn on fine with 3.3!
Breakbeam output: 1.3v drop, 100mA. 2V / 20 ohm = 100mA
solenoid
DISCHARGE
IXTA3N50D2
ZTX718
***need to tune these resistors***
depletion mode
NO SSR



Board: 2 copper layers, 143.9 x 149.3 mm, 119 parts (47 on the bottom side), 102 nets.

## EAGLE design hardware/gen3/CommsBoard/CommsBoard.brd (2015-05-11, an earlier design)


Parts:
C1, C2: .1uF; 0805
C3, C4: 47uF; 1206
C5, C7, C10, C12: 1uF; 0805
C6, C8, C9, C11: .01uF; 0805
EXTRA: 4-POS-DIP; 4-POS-DIP-SMD
FRAME1, FRAME2: FRAME-LETTER; CREATIVE_COMMONS
GEN_3_REV_B: Spring 2015; LOGO
IMU: MPU6050IMUMPU; MPU-6050IMU
LED1, LED2, LED3, LED4, LED5, LED6, LED7, LED9: LED1206; LED-1206
LOGIC_HEADER: M10LOCK; 1X10_LOCK
POWER_HEADER: M10LOCK; 1X10_LOCK
PROG: M05X2PTH; AVR_ICSP
R1, R5, R6, R7, R8, R9, R10, R11, R12, R21: 10k; 0805
R2, R3, R4, R22: 4.7k; 0805
R13, R14, R15, R16, R17, R18, R19, R20: 1k; 0805
ROBID: 4-POS-DIP; 4-POS-DIP-SMD
RX: TEST_PT; TESTING_PT
S1, S2: SWITCH-MOMENTARY-2SMD-4; TACTILE_SWITCH_TALL
SPARE_HEADER: M10LOCK; 1X10_LOCK
SPI_HEADER: M10LOCK; 1X10_LOCK
TSENSE: MCP9700SMD; SOT23-3
TX: TEST_PT; TESTING_PT
U1: ATMEGA165PV-8AU; QFP80P1600X1600X120-64N
XBEE: XBEE-1B1; XBEE-1

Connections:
3.3V: C3.1, C6.1, C7.1, C9.1, C10.1, C11.2, C12.2, EXTRA.5 (4B), EXTRA.6 (3B), EXTRA.7 (2B), EXTRA.8 (1B), IMU.VCC, LOGIC_HEADER.5, LOGIC_HEADER.6, LOGIC_HEADER.7, PROG.2, R1.2, R21.2, ROBID.5 (4B), ROBID.6 (3B), ROBID.7 (2B), ROBID.8 (1B), TSENSE.1 (VCC), U1.21 (VCC_2), U1.52 (VCC), XBEE.1 (VDD)
5V: C4.1, C5.1, C8.1, LOGIC_HEADER.8, LOGIC_HEADER.9, LOGIC_HEADER.10
12V: POWER_HEADER.6, POWER_HEADER.7, POWER_HEADER.8, POWER_HEADER.9, POWER_HEADER.10
12VGND: POWER_HEADER.1, POWER_HEADER.2, POWER_HEADER.3, POWER_HEADER.4, POWER_HEADER.5
BID0: R8.2, ROBID.1 (1A), U1.48 (PA3)
BID1: R7.2, ROBID.2 (2A), U1.49 (PA2)
BID2: R6.2, ROBID.3 (3A), U1.50 (PA1)
BID3: R5.2, ROBID.4 (4A), U1.51 (PA0)
CTS: U1.9 (PE7), XBEE.12 (CTS)
EX0: EXTRA.1 (1A), R12.2, U1.44 (PA7)
EX1: EXTRA.2 (2A), R11.2, U1.45 (PA6)
EX2: EXTRA.3 (3A), R10.2, U1.46 (PA5)
EX3: EXTRA.4 (4A), R9.2, U1.47 (PA4)
FILT: C2.2, R1.1, U1.64 (AVCC)
GLED1: R13.2, U1.35 (PC0)
GLED2: R15.2, U1.37 (PC2)
GLED3: R17.2, U1.39 (PC4)
GLED4: R19.2, U1.41 (PC6)
GND: C1.1, C2.1, C3.2, C4.2, C5.2, C6.2, C7.2, C8.2, C9.2, C10.2, C11.1, C12.1, IMU.GND, LED1.C, LED2.C, LED3.C, LED4.C, LED5.C, LED6.C, LED7.C, LED9.C, LOGIC_HEADER.1, LOGIC_HEADER.2, LOGIC_HEADER.3, LOGIC_HEADER.4, PROG.4, PROG.6, PROG.8, PROG.10, R5.1, R6.1, R7.1, R8.1, R9.1, R10.1, R11.1, R12.1, S1.B2 (2), S2.B2 (2), TSENSE.3 (GND), U1.22 (GND_3), U1.53 (GND_2), U1.63 (GND), XBEE.10 (GND)
INT: IMU.INT, U1.5 (PE3)
MISO: PROG.9, R3.1, U1.13 (PB3)
MOSI: PROG.1, R2.1, U1.12 (PB2)
unnamed: LED9.A, R13.1
unnamed: R22.1, U1.4 (PE2)
unnamed: LED1.A, R14.1
unnamed: LED2.A, R15.1
unnamed: LED3.A, R16.1
unnamed: LED4.A, R17.1
unnamed: LED5.A, R18.1
unnamed: LED6.A, R19.1
unnamed: LED7.A, R20.1
unnamed: C1.2, U1.62 (AREF)
PRE-MISO: R3.2, SPI_HEADER.2
PRE-MOSI: R2.2, SPI_HEADER.1
PRE-SCK: R4.2, SPI_HEADER.3
RESET: PROG.5, R21.1, S1.A2 (1), U1.20 (~RESET/PG5)
RLED1: R14.2, U1.36 (PC1)
RLED2: R16.2, U1.38 (PC3)
RLED3: R18.2, U1.40 (PC5)
RLED4: R20.2, U1.42 (PC7)
RTS: U1.8 (PE6), XBEE.16 (RTS)
RX: RX.P$1, U1.2 (PE0), XBEE.2 (DOUT)
SCK: PROG.7, R4.1, U1.11 (PB1)
SCL: IMU.SCL, U1.6 (PE4)
SDA: IMU.SDA, U1.7 (PE5)
SPARE1: SPARE_HEADER.1, U1.25 (PD0)
SPARE2: SPARE_HEADER.2, U1.26 (PD1)
SPARE3: SPARE_HEADER.3, U1.27 (PD2)
SPARE4: SPARE_HEADER.4, U1.28 (PD3)
SPARE5: SPARE_HEADER.5, U1.29 (PD4)
SS_E1: SPI_HEADER.6, U1.59 (PF2)
SS_E2: SPI_HEADER.7, U1.58 (PF3)
SS_E3: SPI_HEADER.8, U1.57 (PF4)
SS_E4: SPI_HEADER.9, U1.56 (PF5)
SS_E5: SPI_HEADER.10, U1.55 (PF6)
SS_K: SPI_HEADER.5, U1.60 (PF1)
SS_M: SPI_HEADER.4, U1.61 (PF0)
TSENSE: TSENSE.2 (VO), U1.54 (PF7)
TX: TX.P$1, U1.3 (PE1), XBEE.3 (DIN)
XBRST: R22.2, S2.A2 (1), XBEE.5 (RESET)

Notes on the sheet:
extra dip switches
Series 1 Xbee Responsible for communicating forwards and backwards to the main computer
robot ID dipswitches
extra dipswitches for future use
Resistors give priority to programmer over other SPI signals.
There are 3 extra slave select lines in case we add other boards
Runs C++
Programming connector
Boards are stacked vertically and connect through 4 header pins. Comms board / Motor board / Kicker board


Board: 2 copper layers, 140.0 x 100.0 mm, 60 parts (0 on the bottom side), 60 nets.

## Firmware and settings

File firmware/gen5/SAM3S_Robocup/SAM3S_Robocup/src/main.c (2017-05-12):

/**
 * Author: Liam Mulshine 
 *
 * RFC Cambridge Firmware
 */

#include <asf.h>
#include <RobocupDrivers.h>
#include <pins.h>
int pin1 = 0;
int pin2 = 0;
int pin3 = 0;
int pin4 = 0;

// packet in which we should receive the speed commands from comms board
uint8_t speed[4] = {0x00,0x00,0x00,0x00};
// indicate the previous speed commands... use to check if we should update motor speeds
uint32_t prev_speed[2] = {0x00000000,0x00000000};
// buffer that holds up to date speed commands... updated in parse_speeds()
uint32_t speed_buf[2] = {0x00,0x00};
// flag set whenever speed request from comms board is needed
int flag = 0;

void parse_speeds(uint8_t *buf) {
	speed_buf[0] = ((uint32_t) buf[0]) | ((uint32_t) buf[1] << 8);	
	speed_buf[1] = ((uint32_t) buf[2]) | ((uint32_t) buf[3] << 8);	
}

void SysTick_Handler(void) {
	/*
	pin1 = ioport_get_pin_level(FAULTN0);
	pin2 = ioport_get_pin_level(FAULTN2);
	pin3 = ioport_get_pin_level(FAULTN0);
	pin4 = ioport_get_pin_level(FAULTN2);
	ioport_toggle_pin_level(DIR2);*/
	
	// set flag to indicate that we need to read from the comms board in the main loop
	flag = 1;	
}

int main (void)
{
	/* Insert system clock initialization code here (sysclk_init()). */
	sysclk_init();
	board_init();
	pin_config();
	SysTick_Config(sysclk_get_cpu_hz() / 10);

	REG_PWM_FCR = 0;	// clear the pwm fault if you accidentally set pwm period or duty cycle to an bad value :)	

	// configure PWM module to allow for motor speed control
	configure_pwm();
	//configure DAC in order to set kicker reference values later
	configure_dac();
	
	Motor motor0;
	Motor motor1;
	Motor motor2;
	Motor motor3;
	initialize_motor(&motor0,CHANNEL0);
	initialize_motor(&motor1,CHANNEL1);
	initialize_motor(&motor2,CHANNEL2);
	initialize_motor(&motor3,CHANNEL3); 
	
	uint32_t kicker_speed = 15;
	configure_kicker();
	//chip_enable();
	//kick_enable();
	
	configure_twi();
	//configure_io_expander();
	uint32_t new_speed = 1;
    while(1){
		
		if(!ioport_get_pin_level(CHARGE_DONE))
		{
			ioport_set_pin_level(CHARGE,false);
			kick_enable();
		}
		
		if(flag)
		{
			receive_packet(0,0,ARDUINO_ADDR,speed,4*sizeof(uint8_t));	
			flag = 0;
		}
		
		parse_speeds(speed);
		if(speed_buf[0] != prev_speed[0] || speed_buf[1] != prev_speed[1])
		{	
			update_speed(&motor0,speed_buf[0]);
			update_speed(&motor1,speed_buf[1]);
			prev_speed[0] = speed_buf[0];
			prev_speed[1] = speed_buf[1];
			
		}
		
		//send_packet(0,0,ARDUINO_ADDR,speed[0],sizeof(uint8_t));
		// right now we set the kicker reference value each time through the loop. 
		// We may want to change this later on if we find that this is a bottle neck in
		// our control loop
		set_kick_ref(kicker_speed);
		/* Insert application code here, after the board has been initialized. */
	}
}

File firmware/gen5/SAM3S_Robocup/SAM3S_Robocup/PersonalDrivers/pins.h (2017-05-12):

/*
 * pins.h
 *
 * Created: 2/13/2017 2:46:43 PM
 *  Author: Liam James Mulshine
 */ 


#ifndef PINS_H_
#define PINS_H_

#include <asf.h>

#define DISCHARGE IOPORT_CREATE_PIN(PIOA,23)
#define CHARGE IOPORT_CREATE_PIN(PIOB,3)
#define CHARGE_DONE IOPORT_CREATE_PIN(PIOB,2)
#define BREN0 IOPORT_CREATE_PIN(PIOA,10)
#define DIR0 IOPORT_CREATE_PIN(PIOA,9)
#define FAULTN0 IOPORT_CREATE_PIN(PIOA,17)
#define BREN2 IOPORT_CREATE_PIN(PIOA,7)
#define DIR2 IOPORT_CREATE_PIN(PIOA,12)
#define FAULTN2 IOPORT_CREATE_PIN(PIOA,20)
#define DIR1 IOPORT_CREATE_PIN(PIOA,11)
#define BREN1 IOPORT_CREATE_PIN(PIOA,8)
#define FAULTN1 IOPORT_CREATE_PIN(PIOA,19)

void input_change_handle () 
{
	ioport_set_pin_level(DISCHARGE, true);
	uint8_t test[1] = {0};
	//!!!TODO: decode received buffer for each GPIO and perform 
	receive_packet(INTCAPA,sizeof(uint8_t),IO_EXPANDER_ADDRESS,test,sizeof(uint8_t));
	receive_packet(INTCAPB,sizeof(uint8_t),IO_EXPANDER_ADDRESS,test,sizeof(uint8_t));
	receive_packet(GPIOA,sizeof(uint8_t),IO_EXPANDER_ADDRESS,test,sizeof(uint8_t));
	receive_packet(GPIOB,sizeof(uint8_t),IO_EXPANDER_ADDRESS,test,sizeof(uint8_t));
}

void pin_config(void)
{
	ioport_init();
	
	//!!!TODO: Get rid of all unnecessary input/output pins due to introduction of IO-Expander
	// set pin directions
	ioport_set_pin_dir(DISCHARGE,IOPORT_DIR_OUTPUT);			// DISCHARGE - OUTPUT
	ioport_set_pin_dir(BREN0,IOPORT_DIR_OUTPUT);				// BREAK ENABLE - MOTOR 0 (BREN0) - OUTPUT
	ioport_set_pin_dir(BREN1,IOPORT_DIR_OUTPUT);				// BREAK ENABLE - MOTOR 1 (BREN1) - OUTPUT 
	ioport_set_pin_dir(BREN2,IOPORT_DIR_OUTPUT);				// BREAK ENABLE - MOTOR 2 (BREN2) - OUTPUT
	ioport_set_pin_dir(FAULTN0,IOPORT_DIR_INPUT);				// FAULT INPUT - MOTOR 0 (FAULTN0) - INPUT
	ioport_set_pin_dir(FAULTN2,IOPORT_DIR_INPUT);				// FAULT INPUT - MOTOR 2 (FAULTN2) - INPUT
	ioport_set_pin_dir(DIR0,IOPORT_DIR_OUTPUT);					// DIRECTION - MOTOR 0 (DIR0) - OUTPUT
	ioport_set_pin_dir(DIR1,IOPORT_DIR_OUTPUT);					// DIRECTION - MOTOR 1 (DIR1) - OUTPUT
	ioport_set_pin_dir(DIR2,IOPORT_DIR_OUTPUT);					// DIRECTION - MOTOR 2 (DIR2) - OUTPUT
	ioport_set_pin_dir(CHARGE,IOPORT_DIR_INPUT);				// CAP CHARGE - OUTPUT
	ioport_set_pin_dir(CHARGE_DONE,IOPORT_DIR_INPUT);			// CHARGE DONE - INPUT
	
	// set pin mode	
	ioport_set_pin_mode(FAULTN0,IOPORT_MODE_PULLUP);			// FAULTN0
	ioport_set_pin_mode(FAULTN1,IOPORT_MODE_PULLUP);			// FAULTN1
	ioport_set_pin_mode(FAULTN2,IOPORT_MODE_PULLUP);			// FAULTN2
	
	// set initial pin level
	ioport_set_pin_level(DISCHARGE,false);						// DISCHARGE - LOW	
	ioport_set_pin_level(BREN0,false);							// BREN0 - LOW
	ioport_set_pin_level(BREN1,false);							// BREN1 - LOW
	ioport_set_pin_level(BREN2,false);							// BREN2 - LOW
	ioport_set_pin_level(DIR0,false);							// DIR0 - LOW
	ioport_set_pin_level(DIR1,false);							// DIR1 - HIGH
	ioport_set_pin_level(DIR2,false);							// DIR2 - LOW
	ioport_set_pin_level(CHARGE,false);							// CHARGE - LOW	
	
	// enable external interrupts to interface with IO-Expander 
	pmc_enable_periph_clk(ID_PIOA);
	pio_set_input(PIOA,PIO_PA9,PIO_INPUT);
//	pio_set_input(PIOA,PIO_PA20,PIO_INPUT);
	pio_handler_set(PIOA,ID_PIOA,PIO_PA9,PIO_IT_RISE_EDGE,input_change_handle);
//	pio_handler_set(PIOA,ID_PIOA,PIO_PA20,PIO_IT_RISE_EDGE,input_change_handle);
	pio_enable_interrupt(PIOA,PIO_PA9);
//	pio_enable_interrupt(PIOA,PIO_PA20);
	NVIC_EnableIRQ(PIOA_IRQn);
}

#endif /* PINS_H_ */

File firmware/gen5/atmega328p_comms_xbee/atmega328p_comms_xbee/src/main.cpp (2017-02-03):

/*
 * atmega328p_comms_xbee.cpp
 *
 * Created: 1/29/2017 14:46:12
 * Author : Jon Cruz
 */ 

#include "ros.h"
#include "ros_lib/std_msgs/String.h"

extern "C" {
	#include <util/delay.h>
}

// Needed for AVR to use virtual functions
extern "C" void __cxa_pure_virtual(void);
void __cxa_pure_virtual(void);

ros::NodeHandle nh;

std_msgs::String str_msg;
ros::Publisher chatter_test("chatter_test", &str_msg);

char hello[13] = "hello world!";

int main(void)
{
	uint32_t prev_time = 0UL;
	
	// Initialize ROS
	nh.initNode();
	nh.advertise(chatter_test);
	
    while (1) {
		// Send message each second
		if (avr_time_now() - prev_time > 1000) {
			str_msg.data = hello;
			chatter_test.publish(&str_msg);
			prev_time = avr_time_now();
		}
		nh.spinOnce();
    }
	return 0;
}

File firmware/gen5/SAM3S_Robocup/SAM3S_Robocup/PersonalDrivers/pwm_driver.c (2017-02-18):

#include <RobocupDrivers.h>
#include <asf.h>

#define PWM1 IOPORT_CREATE_PIN(PIOA,0)
#define PWM2 IOPORT_CREATE_PIN(PIOA,1)
#define PWM3 IOPORT_CREATE_PIN(PIOA,2)
#define PWM4 IOPORT_CREATE_PIN(PIOA,14) // NOTE the this PWM channel utilizes peripheral B

void configure_pwm(){
	
	// configure pin 0 to respond to peripheral_A PWM
	pio_configure_pin(PWM1,PIO_TYPE_PIO_PERIPH_A);
	// configure pin 1 to respond to peripheral_A PWM
	pio_configure_pin(PWM2,PIO_TYPE_PIO_PERIPH_A);
	// configure pin 2 to respond to peripheral_A PWM
	pio_configure_pin(PWM3,PIO_TYPE_PIO_PERIPH_A);
	// configure pin 14 to respond to peripheral_B PWM
	pio_configure_pin(PWM4,PIO_TYPE_PIO_PERIPH_B); // PWMH3 is part of peripheral B

	// enable PWM module to receive master clock
	pmc_enable_periph_clk(ID_PWM);
}

void update_duty_cycle(uint32_t duty_cycle, Channel chan) {
	// set update duty cycle register to specified duty cycle. Duty cycle will change on next duty cycle period due to double buffering system
	switch(chan)
	{
		case CHANNEL0:
			pwm_channel_update_duty(PWM,&pwm_0,duty_cycle);
			break;		
		case CHANNEL1:
			pwm_channel_update_duty(PWM,&pwm_1,duty_cycle);
			break;
		case CHANNEL2:
			pwm_channel_update_duty(PWM,&pwm_2,duty_cycle);
			break;
		case CHANNEL3:
			pwm_channel_update_duty(PWM,&pwm_3,duty_cycle);
			break;
	}
}

/*
*	Attaches motor struct, m, to the pwm channel specified by the motor struct's channel value and enables the pwm channel. 
*
*/
void attach_motor(Motor *m) {
	
	switch(m->motor_channel){
		case CHANNEL0 :
		
			// disable PWM channel in order to change clock configuration, then initialize PWM module clock details
			pwm_channel_disable(PWM, PWM_CHANNEL_0);

			pwm_clock_t clock_setting_0 = {
				.ul_clka = 0,
				.ul_clkb = 25000 * 1000, // this gives us approximately a 30kHz signal (perfect for the DVR motor controllers which require freq between 16kHz and 50kHz
				.ul_mck = sysclk_get_cpu_hz()
			};
			pwm_init(PWM, &clock_setting_0);
		
			// specify channel settings and initialize
			pwm_0.ul_prescaler = PWM_CMR_CPRE_CLKB;
			pwm_0.ul_period = 1000;
			pwm_0.ul_duty = 100;
			pwm_0.channel = PWM_CHANNEL_0;
			pwm_channel_init(PWM, &pwm_0);
		
			// finally, enable pwm channel
			pwm_channel_enable(PWM, PWM_CHANNEL_0);
			break;
		case CHANNEL1 :
			pwm_channel_disable(PWM, PWM_CHANNEL_1);
			
			pwm_clock_t clock_setting_1 = {
				.ul_clka = 0,
				.ul_clkb = 25000 * 1000,
				.ul_mck = sysclk_get_cpu_hz()
			};
			pwm_init(PWM, &clock_setting_1);

			pwm_1.ul_prescaler = PWM_CMR_CPRE_CLKB;
			pwm_1.ul_period = 1000;
			pwm_1.ul_duty = 500;
			pwm_1.channel = PWM_CHANNEL_1;
			pwm_channel_init(PWM, &pwm_1);
			pwm_channel_enable(PWM, PWM_CHANNEL_1);
			break;			
		case CHANNEL2 :
			pwm_channel_disable(PWM, PWM_CHANNEL_2);
			
			pwm_clock_t clock_setting_2 = {
				.ul_clka = 0,
				.ul_clkb = 25000 * 1000,
				.ul_mck = sysclk_get_cpu_hz()
			};
			pwm_init(PWM, &clock_setting_2);
			
			pwm_2.ul_prescaler = PWM_CMR_CPRE_CLKB;
			pwm_2.ul_period = 1000;
			pwm_2.ul_duty = 500;
			pwm_2.channel = PWM_CHANNEL_2;
			pwm_channel_init(PWM, &pwm_2);
			
			pwm_channel_enable(PWM, PWM_CHANNEL_2);
			break;	
		case CHANNEL3 :
				pwm_channel_disable(PWM, PWM_CHANNEL_3);
						
				pwm_clock_t clock_setting_3 = {
					.ul_clka = 0,
					.ul_clkb = 25000 * 1000, 
					.ul_mck = sysclk_get_cpu_hz()
				};
				pwm_init(PWM, &clock_setting_3);
						
				pwm_3.ul_prescaler = PWM_CMR_CPRE_CLKB;
				pwm_3.ul_period = 1000;
				pwm_3.ul_duty = 500;
				pwm_3.channel = PWM_CHANNEL_3;
				pwm_channel_init(PWM, &pwm_3);

				pwm_channel_enable(PWM, PWM_CHANNEL_3);
			break;			
	}
	
}

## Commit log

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2006-12-23 fixed trunk
    [BLDCdrivesequence.xls, Kicker 12-15-06.sch, brushless.brd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]
2006-12-23 fixed trunk more
    [components.xls, protocol.xls]
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2007-01-21 fixed indenting in brushless worked on transmitting
    [pins.h]
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2007-03-27 branched brushless for hall sensor error correction
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2007-05-12 fixed broken wires
    [kicker3.0.brd]
2007-05-18 Moved filter capacitors on 555 and mosfet driver to a better position.
    [kicker3.0.brd]
2007-05-18 brushless: added resistors to LEDs, added pullups to hall sensors, moved filter to board, connected vss and vso on mosfet driver
    [BLDCdrivesequence.xls, brushless.brd, brushless.sch]
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2007-05-23 made a couple changes to ensure the kicker pnp's are initialized high, but it didn't work
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2007-05-31 fixed minor problems with kicker3.0
    [kicker3.0.brd]
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2007-06-19 corrected hall sequence for new boards
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2007-06-29 started encoder feedback, still doesn't really work
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2007-10-30 fixed regulator layout, still needs a bit more work
    [robocup-switcher board.brd, robocup-switcher board.sch]
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2007-11-05 Deleted unused kicker board.brd and kicker board.sch files that clark had made because kick_test is the actual one we're useing
    [kicker board.brd, kicker board.sch]
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2007-11-22 Update brushless part list and add values of individual components on eagle files
    [A3938.brd, A3938.sch, brushless_test.brd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]
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2007-12-02 made a few adjustments ot the parts list, and changed to a total resisitor and capacitor list
    [components.csv]
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2008-03-05 Added 06-07 brushless boards to replace brushless_test's because they won't be used
    [brushless.brd, brushless.sch]
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2008-03-16 continued working on the motherboard made driver 1 complete and correct
    [motherboard.sch]
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2008-03-23 Fixed the DRIB connection
    [Aux_kicker.brd, Aux_kicker.sch]
2008-03-23 corrected transformer, changed discharging mosfet package, and added discharge button in schematic
    [kicker.brd, kicker.sch]
2008-03-23 put in ground and fixed an obvious line overlap
    [Aux_kicker.brd]
2008-03-23 Updated motherboard got brushless done, gyro done and radios except for antenna.
    [motherboard.sch]
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2008-03-23 Added motherboard board template with holes and overall dimensions, created in freeware Eagle. I'm not sure where the tabs are supposed to go. --Walker
    [motherboard.brd]
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2008-03-24 updated motherboard. added pads for breakbeams, buffer circuits for caps and batt voltage, and the usb interface.
    [motherboard.brd, motherboard.sch]
2008-03-25 corrected motherboard size --Walker
    [motherboard.brd, motherboard.sch]
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2008-03-27 fixed up front
    [motherboard.brd, motherboard.sch]
2008-03-27 worked on board. fixed a couple things in the schematic
    [motherboard.brd, motherboard.sch]
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2008-03-27 fixed back --Walker
    [motherboard.brd]
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2008-04-25 Back side was missing a trace. KYLE!!!!!!!!!
    [Aux_kicker.brd]
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2008-05-01 determined "scaled" pid code is jittery
    [main.c]
2008-05-04 Added Auxillery Kicker code (that doesn't work yet)
    [pins.h]
2008-05-04 Changed value of r10 to be 10K, because otherwise the pic can't be programmed
    [Aux_kicker.brd, Aux_kicker.sch]
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2008-05-05 aux. kicker code is working. Whether pins are high or low may not be exactly correct, but stuff toggles. Chip kicker isn't used at all.
    [pins.h]
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2008-05-08 Walker moved a couple traces apart on Aux_kicker.brd and moved the screw holes to more appropriate locations on motherboard.brd
    [Aux_kicker.brd, motherboard.brd]
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2009-01-21 Changed antenna connector to Digikey part and added mosfet driver to list of parts to order
    [Fall 2008 Robocup Orders.xls]
2009-01-24 fixed some brushless bugs
    [main.c]
2009-02-08 Fixes for the aux kicker.
    [pins.h]
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2009-03-01 Added file to keep track of the status of brushless boards and to try and track the problems
    -Ben
    [brushless state.ods]
2009-03-01 added error capping to fix jerky acceleration and left strafing, modified PID constants, and added test dead reckoning function (not working)
    [main.c]
2009-03-15 made some not connected things look less connected. I don't think the board changed at all
    [kicker.brd, kicker.sch]
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2009-05-17 added comment that mosfet driver isn't an inverter, even though that's the symbol in the schematic.
    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
    [Aux_kicker.sch]
2009-06-30 added feed forward term to CS199r/wheels/main.c.
    Changed/fixed breakbeam logic, so the command starts charging and then kicks as soon as it sees the ball. Does not always kick after 2 seconds. In trunk/firmware/Auxillery Kicker/mainLogic.c
2009-09-28 Fixed encoder spewing. The SPEW_ENCODER flag is currently NOT taken into account -- the thing always spews.
    [main.c]
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2009-11-08 started making changes to motherboard and brushless board, got some of the header pinouts changed appropriately
    [brushless.brd, brushless.sch, motherboard.brd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]
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2009-11-10 Continued laying out the brushless board. Got rid of the 555 on the Aux. kicker, added a 0603x4 resistor to rfc.lbr
    [Aux_kicker.brd, Aux_kicker.sch, brushless.brd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]
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2009-11-15 fixed the brushless commutation code in cs199r/wheels the backwards commutation was wrong. I also switched back to the May version of PID
    [Aux_kicker.brd, Aux_kicker.sch, brushless.brd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]
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2009-11-19 continued laying out brushless added diodes accross gate resistors, and increased bootstrap capacitors
    [brushless.brd, brushless.sch]
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2009-11-20 added CAO connection to pic, so can monitor current in PIC if we want
    [brushless.brd, brushless.sch]
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2009-11-22 updated the auxillery kicker pinouts to match the new scheme. Moved op amps for capacitor and battery voltage onto aux. kicker and of of the mother board.
    [Aux_kicker.brd, Aux_kicker.sch, motherboard.brd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]
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2009-11-27 Switched order of hall pins on brushless to match motherboard, arranged silkscreens on aux. kicker
    [Aux_kicker.brd, Aux_kicker.sch, brushless.brd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]
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2009-12-12 fixed some stuff on the motherboard
    [motherboard.brd]
2009-12-16 Added Revision numbers and text boxes to motherboard, aux. kicker and brushless. Connected the two grounds together on the motherboard.
    [Aux_kicker.brd, brushless.brd, motherboard.brd]
2009-12-16 movedpin labels on kicker onto the backside of the board and added a silkscreen around the edges
    [Aux_kicker.brd, Aux_kicker.sch, kicker.brd]
2009-12-16 added silk screen saying how to short gyro board
    [motherboard.brd]
2009-12-16 consolidated boards into one board to prepare for ordering, moved some of the silkscreen layers, so the values wouldn't change
    [order2.brd]
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2010-01-12 Rui - changes to trunk firmware: fixed incorrect pin assignments on auxillery kicker pins header file and assignments for unused pins removed code for unused pins and added code for maintaining capac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
    [kicker.brd, kicker.sch]
2010-01-17 changed brushless programming header to be correct. Added traces for ground of brushless ID's that were forgotten before.
    [Aux_kicker.brd, Aux_kicker.sch, brushless.brd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]
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2010-01-20 Rui -- revised kicker board to reduce height to same height as other boards, moved header pins more to center, added room for power resistor, removed snubber circuit (not needed from measurements), o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
    [kicker.brd, kicker.sch]
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2010-01-20 Rui -- moved switching mosfet on kicker board to give clearance with transformer
    [kicker.brd]
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2010-01-22 Fixed programming header and made pots easier to access
    [Aux_kicker.brd, Aux_kicker.sch]
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2010-01-22 removed resistors between fet driver and pic on brushless. Tidied up Aux kicker, centered header pins.
    [Aux_kicker.brd, brushless.brd, brushless.sch]
2010-01-23 moved the radios apart and removed the gyro header on the motherboard. Fixed a couple little things onthe brushless
    [brushless.brd, motherboard.brd, motherboard.sch]
2010-01-23 finished spreading out the radios. Added more room between front two brushless and returned to the original amount of room between the kicker and nearest brushless.Moved the MB led out farther.
    [brushless.brd, motherboard.brd]
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2010-01-23 updated the order2.brd file for the new boards. Deleted all Dimension lines except the outer one and added little connecting rectangles to try and trick them into thinking it's one board, so there's 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
    [brushless.brd, kicker.brd, order2.brd]
2010-01-23 actually the order to use, didn't put names and values in other layers, so they got screwed up, but should be good now.
    [order2.brd]
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2010-01-26 Resotred components.csv to the new list and added brushless surface mount fet
    [components.csv]
2010-01-26 corrected Fet part number.
    [components.csv]
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2010-06-05 switched 0/1 broken/not broken of breakbeam sensor in code so works. Also redid dribbler code slightly, since PWM is active now, so dribbler works.
2010-10-03 "Merged with CS199r" This is now the version with the minor loop velocity controllers for the wheels (like in Singapore) and with Error checking code.
    [main.c]
2011-01-20 minor LED changes, and an unused fixed position function added by someone for debugging the twitching wheels.
    [main.c]
2011-01-27 baud rate change in bemixnet.c. Increase to around 43k. fixed breakbeam problem receiver not seeing ir led after kicking.
    [pins.h]
2011-01-27 Added two lines of code initializing POSCNTH = 0x80 and POSCNTL = 0x00; So they are initialized to the correct middle value for counting what comes in from the encoders. THIS FIXES TWITCHING!!!
    Also always clear the lowest 2 bits of the duty register PDCnL, since they effect what Q clock things happen on, and should be consistent and probably not change based on the value of duty.
    [main.c]
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2011-01-27 added back in a delay on start up for the motor. It's commented out, but it's there. It doesn't help twitching which is still present sometimes.
    [main.c]
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2011-02-26 Added new smd proximity sensor to rfc.lbr. And added boards for it to interface with the current aux kicker.
    [proximity.brd, proximity.sch]
2011-02-26 Shrunk the pads a little on the SMD package for the proximity sensor to try and make it more machinable on the Modela in the media lab. Finished the board layout.
    [proximity.brd, proximity.sch]
2011-02-27 added functionality in aux kicker firmware to measure cap voltage, added PWM to dribbler, removed PWM from old break beam LED
    [Aux_kicker.sch]
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2012-11-18 Updated aux kicker code to work with two-part break beam. Can be programmed and can receive commands.
    There was an issue that programmed boards could not receive commands,
    which was traced back to changes in the bemixnet.c code regarding
    checksums, which was not working. Perhaps the checksum was off on each
    packet, which caused the aux kicker boards to discard everything. Also
    added to the no_false_positives.c code was a grace period (of 5 main
    loop iterations) for the break beam receiver to react after the LED
    turned on. This was to resolve the issue that the robot would kick on a
    break beam command even when the break beam was seemingly not broken.
2012-12-10 Added hysteresis in breakbeam kick and increased lag after kick
    We noticed that the robot would kick when it seemed like the LED did
    not toggle indicating that the break beam was broken. We hypothesized
    that this was due to the break beam being broken for a split second
    causing the kick. We thus added a hysteresis variable in the break beam
    code in which the break beam must be broken for HYSTERESIS_VALUE number
    of main loops before the robot considers it triggered.
    We also noticed funny noises after the robot kicked once, causing the
    robot to not be able to charge up the capacitors again. This is most
    likely due to the SCRs on the kicker board not turning off immediately
    after kicking befor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
2013-01-20 We found that the breakbeam was not working because the PWM frequency of the BB emitter was modified. Restored it to it's original value, so that it works again. Dribbling capabilities should also be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
2013-02-23 Breakbeam Fixes in Aux Kicker Code
    Changed timing of LED emitter in break beam to match datasheet spec.
    Added counter (breakbeam_count_outer) to reset the break beam every ~4
    sec in case it becomes stuck. Changed break beam trigger condition to
    consider the break beam as not broken if it is ever not broken in a
    burst period. Reduced hysteresis value to account for decreased burst
    period (may not need hysteresis anymore due to combination of trigger
    condition and grace period).
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2013-04-21 Added Brushless Firmware to Test Encoder
    This firmware lets us test how many counts the encoder is putting out
    per revolution of the wheel, in order to determine whether the encoder
    is dirty/broken without having to first remove the encoder assembly.
    To use, open MPLAB and in the Brushless project, replace the main_v2.c
    file with main_v2_encodertest.c (remove the main_v2.c file from the
    project and add main_v2_encodertest.c). Then click on the hammer/broom
    icon at the top and select "Clean and Build for Debugging." Then
    connect the programmer to the brushless board inserted in the position
    corresponding to the motor you want to test, and turn on the robot.
    Click on the download to chip icon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
2013-10-27 Set max duty cycle to half. Fixed overflow in PID.
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2014-11-26 Fixed Erik's comments on Kicker Board.
    [KickerBoard.sch]
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2014-12-06 fixed some comments
    [KickerBoard.sch]
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2014-12-06 Fixed voltage divider.
    Changed resistor from 348K to 100K to change voltage divider from 12V to
    3V.
    [KickerBoard.sch]
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2015-01-14 found actual atmega part, correct footprint
    [CommsBoard.brd, CommsBoard.sch]
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2015-01-14 good layout! problem with vias
    [CommsBoard.brd]
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2015-03-12 fixed ERCs on all boards
    [CommsBoard.sch, KickerBoard.brd, KickerBoard.sch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]
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2015-03-14 fixed current limiting
    [CommsBoard.brd, CommsBoard.sch, KickerBoard.brd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]
2015-03-14 most packages replaced
    [CommsBoard.brd, CommsBoard.sch, MotorBoard.brd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]
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2015-03-20 correct package for comparator
    [MotorBoard.brd, MotorBoard.sch]
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2015-03-22 fixed weird package issues
    [CommsBoard.brd, KickerBoard.brd, KickerBoard.sch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]
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2015-03-24 correct breakbeam circuit
    [KickerBoard.sch]
2015-03-24 fixed diff amp. again
    [MotorBoard.brd, MotorBoard.sch]
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2015-03-27 added buffer and flipped hystereses
    [KickerBoard.brd, KickerBoard.sch]
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2015-03-28 Swapped ports for quad encoders
    [MotorBoard.brd, MotorBoard.sch]
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2015-03-28 Revert "fixed merge"
    This reverts commit a3a9d2be9eb73318679e4322dc627419ee6a78f8, reversing
    changes made to cc6a6570ab89a01d923762550cceb63ea8b9506a.
    [KickerBoard.brd, MotorBoard.brd, MotorBoard.sch]
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2015-03-28 Flipped ports d and e on motor board
    [MotorBoard.brd, MotorBoard.sch]
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2015-03-30 fixed OP3 and OP4 mistake and cluttered inboxes
    [MotorBoard.brd, MotorBoard.sch]
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2015-03-30 fix regulator grounding
    [KickerBoard.sch]
2015-03-30 fixed kicker merge
    [KickerBoard.brd, KickerBoard.sch]
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2015-03-31 fixed voltage values on kicker
    [KickerBoard.brd, KickerBoard.sch]
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2015-03-31 DRC fixes for mtor
    [MotorBoard.brd, MotorBoard.sch]
2015-03-31 fixed all DRC. vias in pads are ok, right?
    [MotorBoard.brd, MotorBoard.sch]
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2015-05-02 fixing board with new switch
    [CommsBoard.brd, CommsBoard.sch]
2015-05-03 fixed slave select issues
    [KickerBoard.brd, KickerBoard.sch, MotorBoard.brd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]
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2015-05-04 fixed trapped signals
    [KickerBoard.brd]
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2015-05-04 working on motor DRC errors
    [KickerBoard.brd, MotorBoard.brd, MotorBoard.sch]
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2015-05-09 Fixed up a switch statement in motorboard
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2015-05-25 Fixed types on setBit and used setBit to fix motorboard problems
2015-05-25 Added motorboard pin names and fixed naming conflict created with PWM typedef
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2015-05-30 Fixed incorrect bit twiddling in the ADC
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2015-06-09 weird linking errors after adding more defines
    [KickerBoard.brd, KickerBoard.sch]
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2015-06-16 Made include files for PID and QEI classes, created very rough skeleton for Motor (still need to fix up PID and QEI classes)
2015-06-16 Fixed motor class so that it compiles (oops)
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2015-06-20 Added default output and pin settings to the motorboard, fixed dependency issues caused by board project not including EELib as a library
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2015-06-22 Fixed most of the input/output PIN/PORT problems in the header files
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2015-07-01 Moved setDirection from motorboard to motor and fixed Motorboard compiler errors from handleCommand
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2015-11-29 Motor Module redesign
    Added new MC, and new driver IC.
    [MotorBoard .sch, MotorBoard.brd]
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2015-11-29 Fixed transistor connection on kicker
    Still need values for resistor
    [KickerBoard.sch]
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2015-12-09 fixed up motor MC
    [MotorBoard.sch]
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2016-02-09 Few overlap edits
    Also need to fix qfn package part, the part needs a smt pad added.
    [MotorBoard.brd]
2016-02-09 Slight fixes
    fixed qfn package and overlap
    [MotorBoard.brd, MotorBoard.sch]
2016-02-13 fixed overlaps, nearly finished routing
    [MotorBoard.brd, MotorBoard.sch]
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2016-02-13 Revert "fixed overlaps, nearly finished routing"
    This reverts commit 58b1fdd4e09a09fd026863b48e748c651eb8a543.
    [MotorBoard.brd, MotorBoard.sch]
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2016-02-21 Added test points
    Placed test point + overlap errors
    [KickerBoard.brd, KickerBoard.sch]
2016-02-27 control board fixes
    Pull up changed, connector added
    [ControlModule.brd, ControlModule.sch]
2016-02-27 fix consistency error
    [ControlModule.brd]
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2016-03-31 motor board v2 done
    things to do, address clearance and maybe change min trace width
    [MotorBoard.brd, MotorBoard.sch]
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2016-03-31 actually fixed merge conflict
    [KickerBoard.brd]
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2016-04-03 finished routing... still need to do error checking
    [ControlModule.brd]
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2016-04-09 motor board fix
    final changes
    [MotorBoard.brd]
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2016-04-10 motor and kicker fixes
    [KickerBoard.brd, MotorBoard.brd]
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2016-04-11 few fixes
    unconnected wires
    [KickerBoard.brd, KickerBoard.sch]
2016-04-12 fixed overlaps
    [ControlModule.brd]
2016-04-13 motorboard and kickerboard ordered thanks caffeine
    fixes include: overlaps, adding mounting points panelizing and
    gerberfiles,, and clearance issues.
    [KickerBoard.brd, MotorBoard-panel.brd, MotorBoard.brd]
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2016-05-18 fixing motorboard
    [MotorBoard.brd, MotorBoard.sch]
2016-05-18 pdi fix
    [ControlModule.brd]
2016-05-18 redid debug connector on comms, but clearance checks havent been done
    [ControlModule.brd, ControlModule.sch]
2016-05-19 motor board 5v error updated
    [MotorBoard.brd]
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2016-05-19 fixed up motor board a bit more
    [MotorBoard.brd, MotorBoard.sch]
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2016-05-22 motor board fixes
    [MotorBoard.brd, MotorBoard.sch]
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2016-05-22 push button fix
    [MotorBoard.brd, MotorBoard.sch]
2016-05-22 fixed pushbutton on comms board
    [ControlModule.brd, ControlModule.sch]
2016-05-23 motor board push button fix
    [MotorBoard.brd, MotorBoard.sch]
2016-05-23 fixed ten thousand net issues on motorboard
    [MotorBoard.brd, MotorBoard.sch]
2016-05-23 fixed all clearance issues on motorboard, stop mask still to go
    [MotorBoard.brd]
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2016-05-23 fixed clearance issues on motorboard again
    [MotorBoard.brd, MotorBoard.sch]
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2016-05-24 fixed minor detail about capacitor sizes (using 0.01uF everywhere instead of .01uF on comms)
    [ControlModule.brd, ControlModule.sch]
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2016-05-25 motorboard ground connections fixes
    [MotorBoard.brd]
2016-05-25 an experiment with ground connections on motorboard - reverse if necessary
    [MotorBoard.brd]
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2016-05-25 fixed SPI connnections
    [ControlModule.brd, ControlModule.sch]
2016-05-25 new sizes + fixes
    [KickerBoard.brd, KickerBoard.sch]
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2016-05-27 mainboard done w errors
    [KickerBoard.brd]
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2016-05-27 few fixes
    [KickerBoard.brd]
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2016-05-31 gerber fix
    [bmask.GBS, bot.GBL, bsilk.GBO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]
2016-06-02 more fixes
    [ControlModule.brd, KickerBoard.brd, MotorBoard.brd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]
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2016-11-17 fixed power supply on LM311
    [KickerBoard.brd, KickerBoard.sch]
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2016-12-01 Working through DRC Errors. Need to look into tolerances of PCB fab.
    [KickerBoard.brd, KickerBoard.sch]
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2016-12-04 fixed clearance issues. all traces at least separated by 8 mils
    [KickerBoard.brd]
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2016-12-13 small fix to control module gnd
    [ControlModule.brd, ControlModule.sch]
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2016-12-20 Added correct border +small fixes
    Added correct border
    Added logo
    Fixed one large capacitor had a very thin wire connecting it to the
    other one.
    Added mounting holes
    NO more clearance errors
    [KickerBoard.brd, KickerBoard.sch]
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2016-12-23 few minor motor board fixes
    [MotorBoard.brd, MotorBoard.sch]
2016-12-23 fixed an accidental change to main board
    [KickerBoard.brd, KickerBoard.sch]
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2017-01-11 added motorboard gerbers, but noticed some potential issues with grounding afterwards. Checking into it now. It appears that the commsboard is ready to go, however
    [ControlModule.brd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]
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2017-01-29 added a file i missed
    [RequestMessageInfo.h, RequestParam.h, RequestServiceInfo.h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]
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2017-03-26 swapped motorboard traces for hallout signals
    [MotorBoard.brd, MotorBoard.sch]
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2017-03-27 Revert "for lev and daniel"
    This reverts commit 2ad717e832d237175bcf1ebd5d5df5283078cebd.
    [KickerBoard.brd]
2017-03-27 Revert "Here, John"
    This reverts commit bab4b26ca5c3038870692d5b09145efa6423a8e6.
    [KickerBoard.brd]
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2017-11-12 replaced motor connectors, still need to be routed
    [KickerBoard.brd, KickerBoard.sch]
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2018-02-02 fixed merge conflict
    [KickerBoard.brd, KickerBoard.sch]
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2018-02-10 Revert "lol"
    This reverts commit 7ea1eec36b27b6c1426725fe18246370710574c2.
    [MotorBoard.brd]
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2018-02-11 redesigned motorboard 30~ traces to go
    [MotorBoard.brd, MotorBoard.sch]
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2018-02-12 finished routing no errors
    [MotorBoard.brd]
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2018-02-12 add motorboard as a part and finsihed all routing, no more 'ignoreable issues'
    [KickerBoard.brd, KickerBoard.sch, MotorBoard.brd]
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2018-04-17 fixed wires for assembly
    [MotorBoard.brd]
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

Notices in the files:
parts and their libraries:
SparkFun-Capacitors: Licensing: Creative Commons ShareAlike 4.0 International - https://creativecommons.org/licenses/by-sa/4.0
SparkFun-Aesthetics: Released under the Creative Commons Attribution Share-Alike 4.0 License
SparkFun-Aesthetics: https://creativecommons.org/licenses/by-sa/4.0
